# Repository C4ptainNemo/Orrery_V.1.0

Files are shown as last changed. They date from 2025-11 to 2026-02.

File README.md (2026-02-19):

# Orrery Version 1
orrery_v1
orrery_v1_no_top
orrey_v1_no_top_labeled

This repository is used to showcase the first completed version of my orrery.

The planets move on what is in escense slew rings, i.e. bearings with one of the rings having gear teeth to allow it to be driven. There are four sets of rings, each having a static ring that is mounted to the base, and two rotating rings, one per planet. These four sets of two make up the eight planets, Mercury & Venus, Earth & Mars, Jupiter & Saturn, Uranus & Neptune.

The gearing for the planets is also divided into the inner and outer planets. This is due to the large difference between their orbital periods. There is a main driving gear which meshed with different sets of gears that give the correct reduction to have accurate oribital periods. The outer planets have an additional planetary gear reducer (26 times reduction) between the main driving gear and their input gears.

---

## Thoughts and Improvements
Since each planets reducing gears are independent of each other, finding the correct gear ratios is simple, with a brute force check of combinations working fine. However this means that there are a lot of gears, since each planet has 3-5 gears to give the reduction and spacing needed. Improvements can be made to the layout of the gears to reduce the need for idler gears. 

Due to uncertaity of the ability to 3D print bevel gears, spur gears were used for the planet rings themselves. This added the limitation that there needs to be space between the adjectent rings to fit planet rings driving gear, which meant the planet ring gears were much larger than they otherwise need to be. Testing to find suiatble methods of printing bevel gears should be done to remove this issue.

A thought I had to reduce the number of gears needed is to have the reduction happen in a chain, instead of having seperate sets of gears for each planet. The difference in period between adjecent planets is around 2-3 except Mars to Jupiter which is about 6:1. So the orbital periods of each planet would be normalised by dividing its orbital period by Mercurys (so Mercury has a period of 1). So by doing the reduction in a chain, an approximately 2:1 reduction is needed coming from Uranus for Nepotune instead of 700:1.

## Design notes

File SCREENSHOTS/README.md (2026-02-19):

### Driving Gears
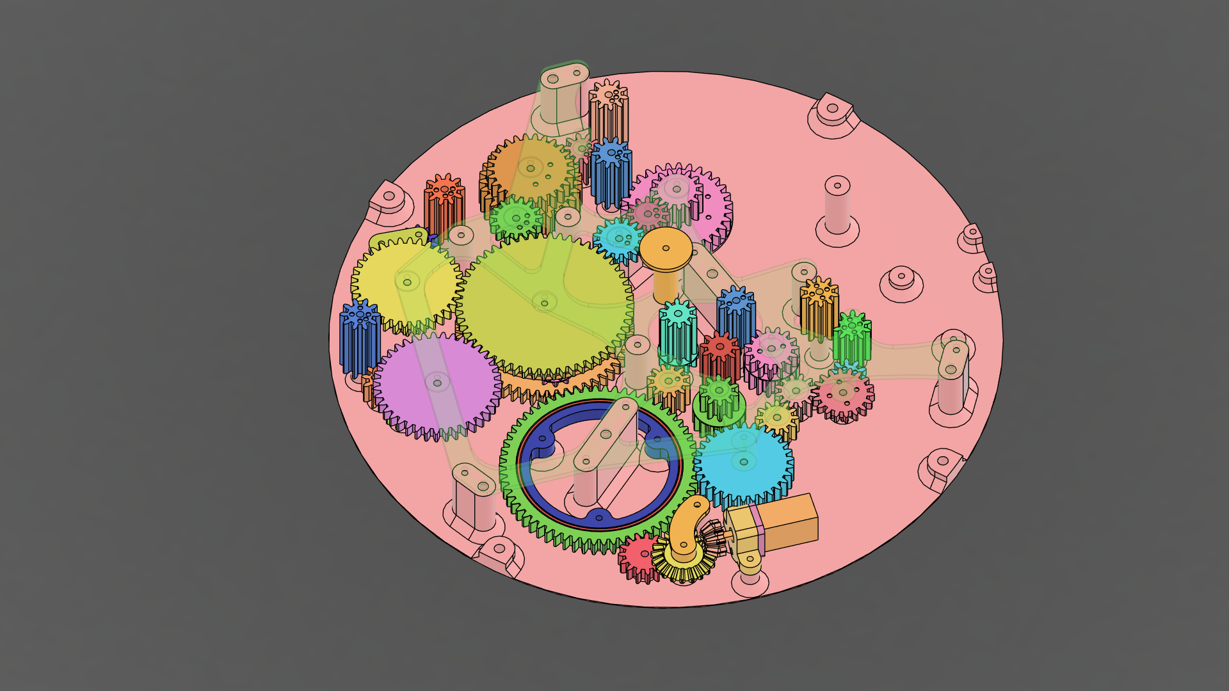
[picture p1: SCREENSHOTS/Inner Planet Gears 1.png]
Inner Planet Gears 1

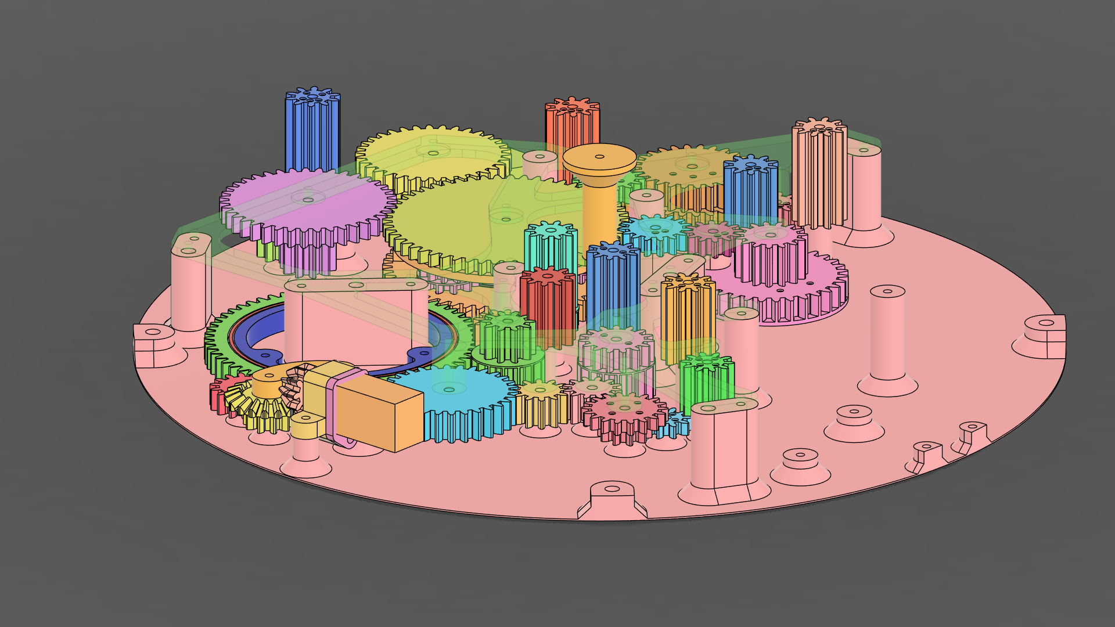
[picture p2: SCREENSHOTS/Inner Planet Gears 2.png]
Inner Planet Gears 2

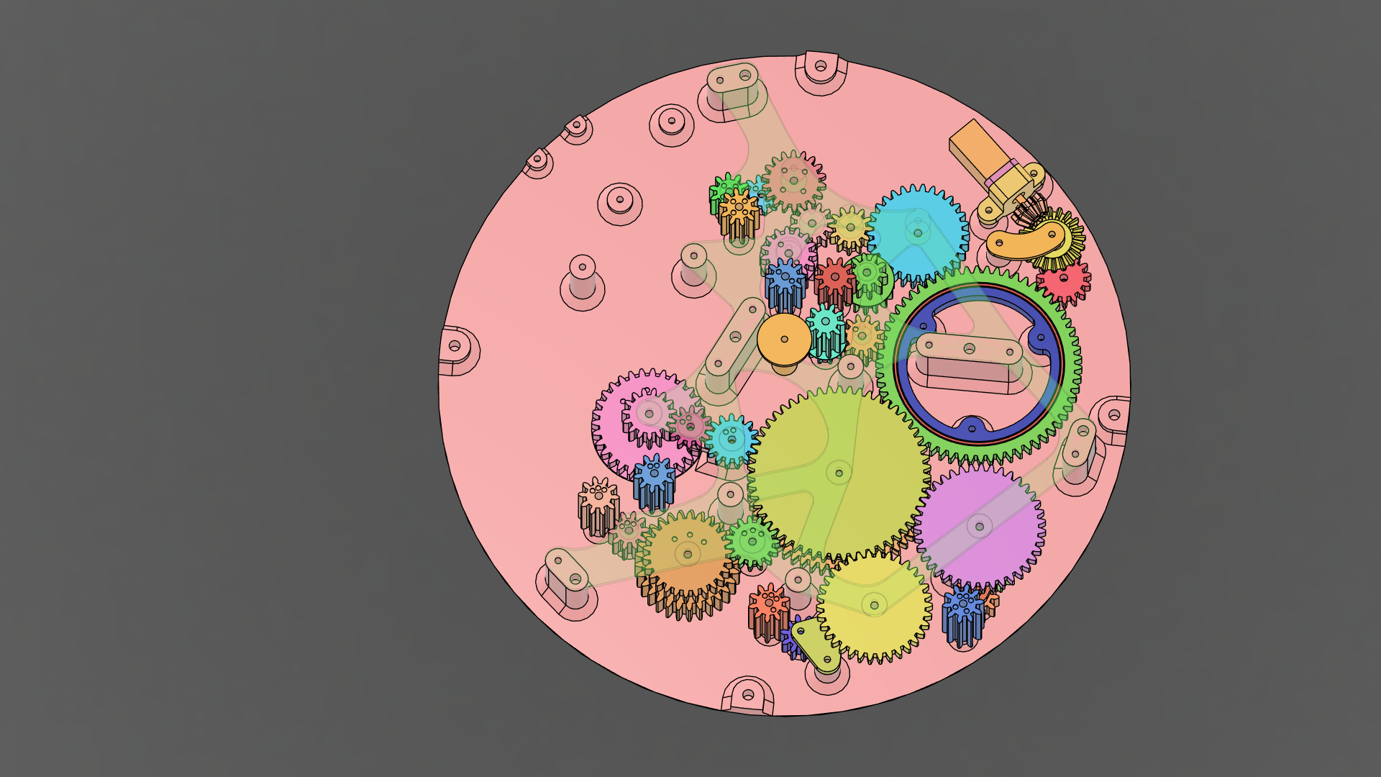
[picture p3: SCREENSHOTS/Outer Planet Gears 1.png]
Outer Planet Gears 1

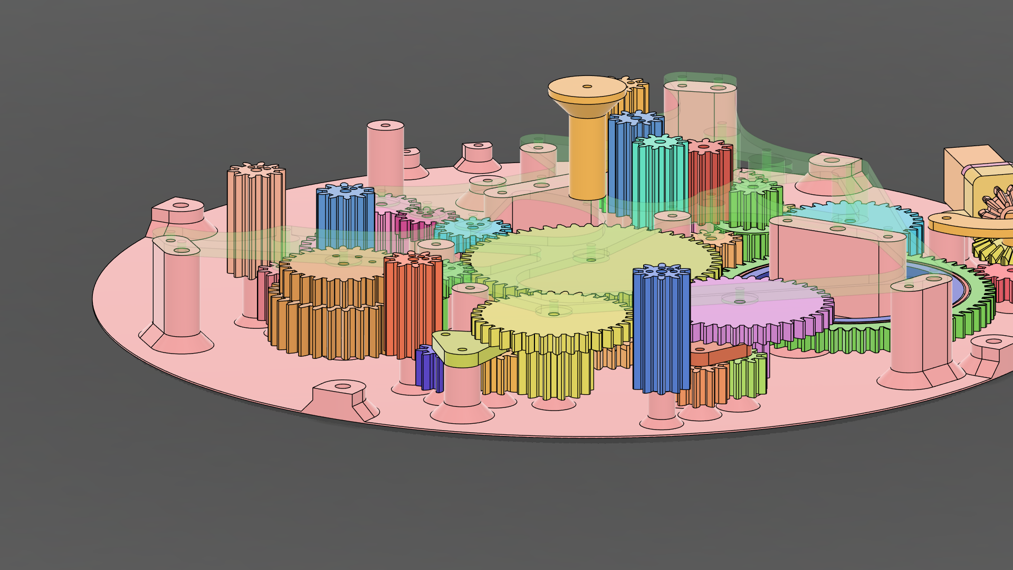
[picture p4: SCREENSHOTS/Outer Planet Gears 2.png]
Outer Planet Gears 2


---

### Ring Gears
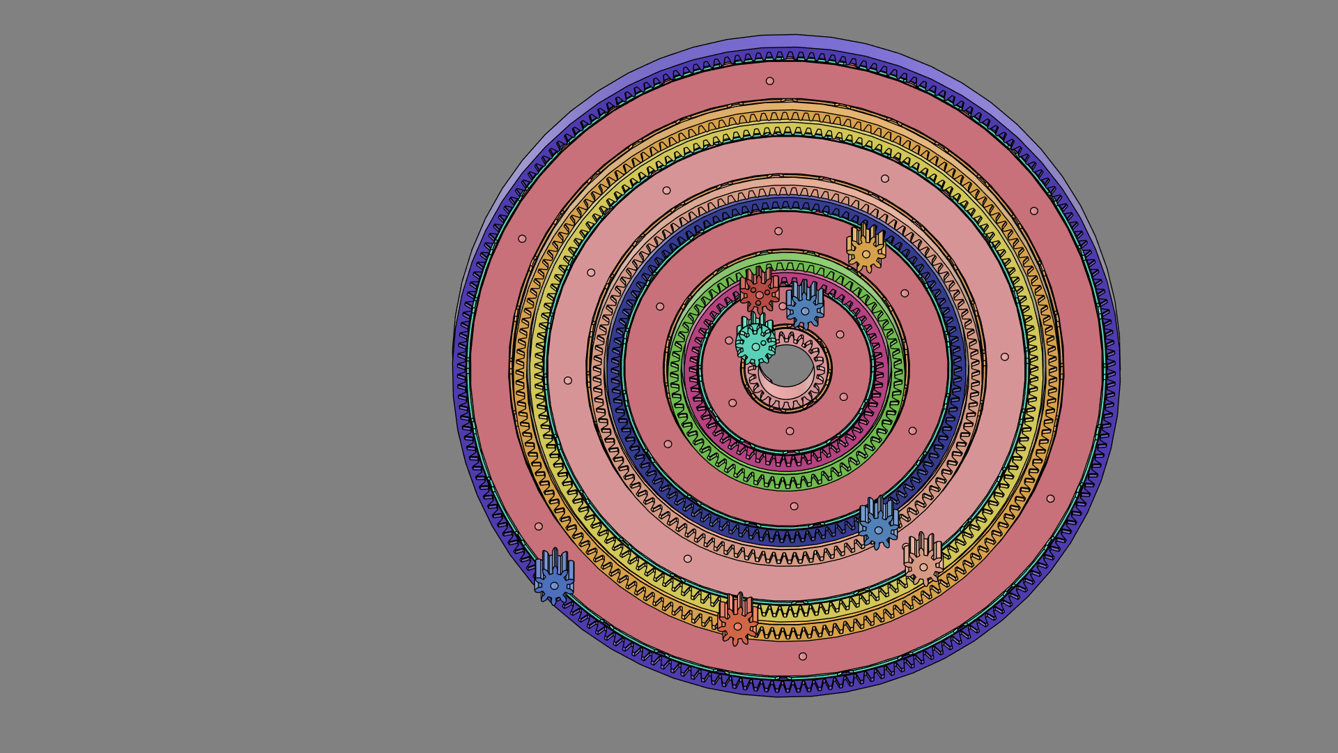
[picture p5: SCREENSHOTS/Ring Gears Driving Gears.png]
Ring Gears Driving Gears


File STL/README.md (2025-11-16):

# Orrery STL Files

## Notes and Thoughts on each type of parts

### Gears
The exteral spur gears were generated by using Fusion360's inbuilt spur gear tool and the modifying the models. The compund gears were simple, by joining two different gears into one part.

The planet ring gears were generated using a community tool {add name of tool}. These were then merged with the templete file for the ring gear assembly.

### Ring Gear Assemblies
The ring gear assembelies were made using a templete assembly that has four configurations, for Mercury & Venus, Earth & Mars, Jupiter & Saturn, Uranus & Neptune.
The configured assembly was imported into a new file and the required internal gears were joined to the appopriate blank inner and outer rings.
This didn't feel like the best way to do this. A better way would probably have been just modelling each geared ring as an indivdual part and then importing into the assembly.

The size of the rotating rings was to be as narrow as possible while allowing for a 1-1.5 modulus involute internal spur gear profile. The static rings were then sized to fill up the remaining space, so that there in as little gap as possible between the rings.
After completing the build I found it nice to watch the gears rotate. Since this is something designed to be looked at, covering the gears by having no gap between rings was definately a mistale. Each ring should be as narrow as possible to allow for the best viewing of the gears inside.

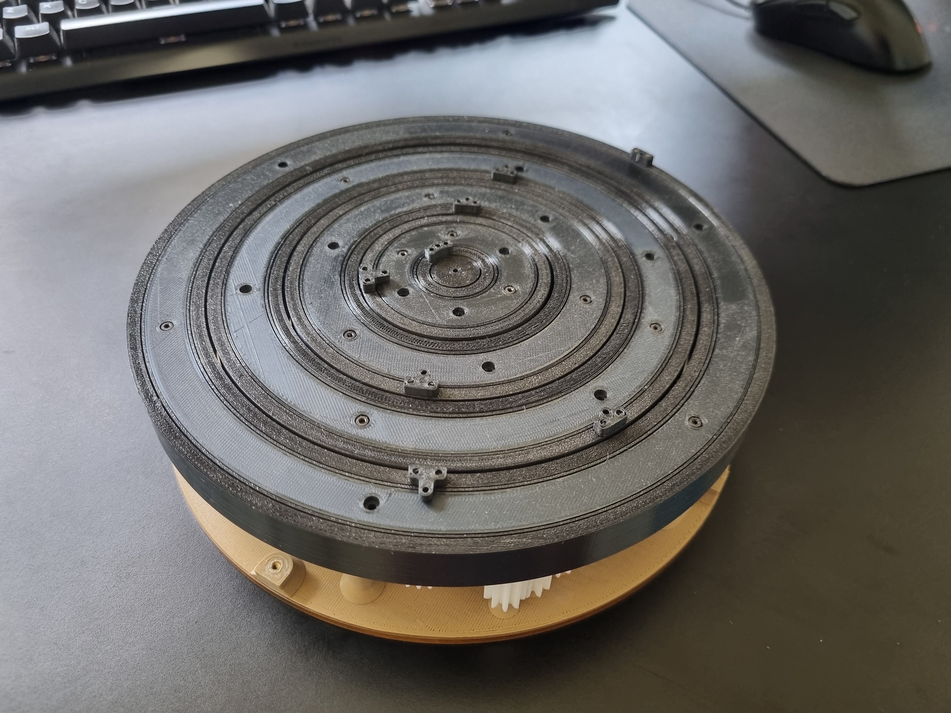
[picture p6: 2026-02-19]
PICTURES & VIDEOS/orrery_v1.jpg

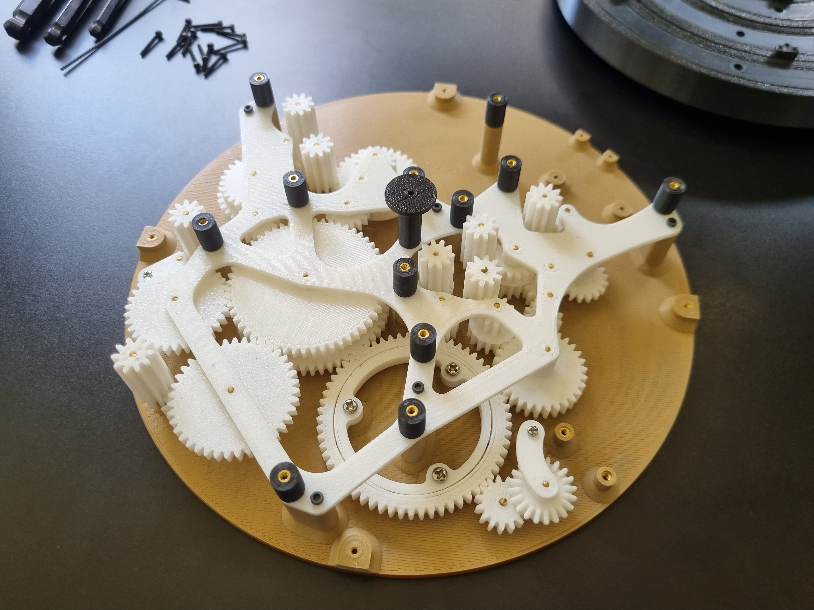
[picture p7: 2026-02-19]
PICTURES & VIDEOS/orrery_v1_no_top.jpg

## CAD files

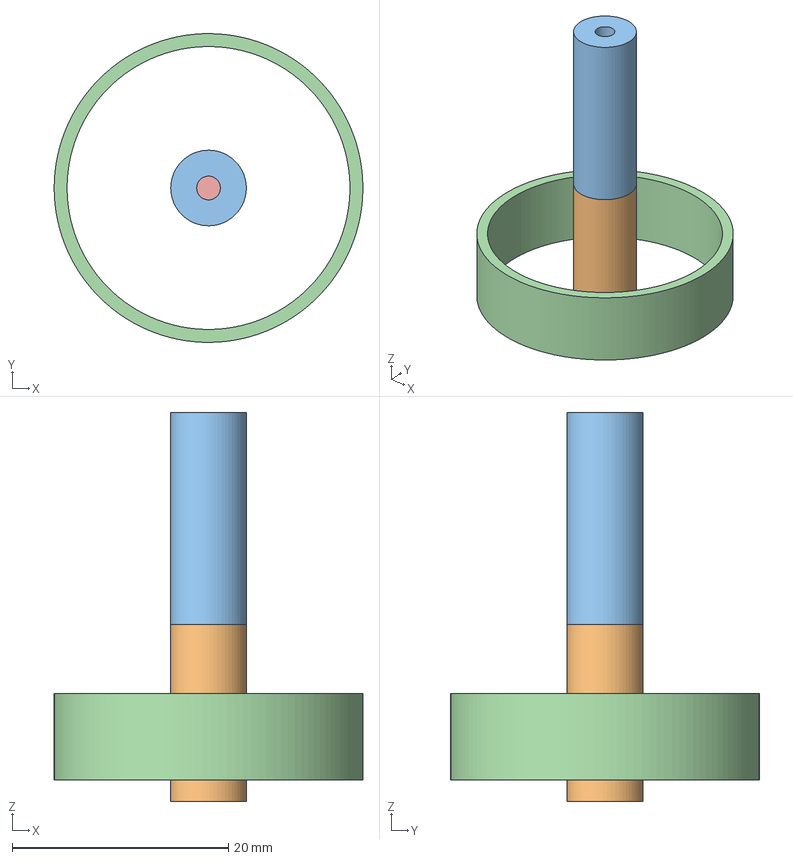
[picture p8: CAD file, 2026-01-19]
STL/Misc Assembly Tools.3mf
28.6 x 28.6 x 36.0 mm

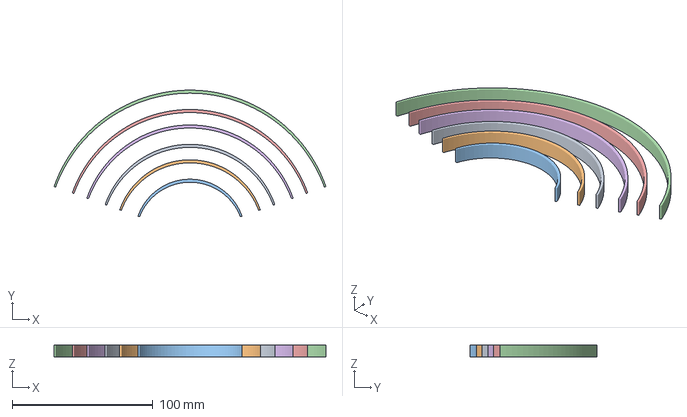
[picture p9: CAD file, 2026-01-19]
STL/Planet Ring Assembly Guides.3mf
193.2 x 90.0 x 8.80 mm

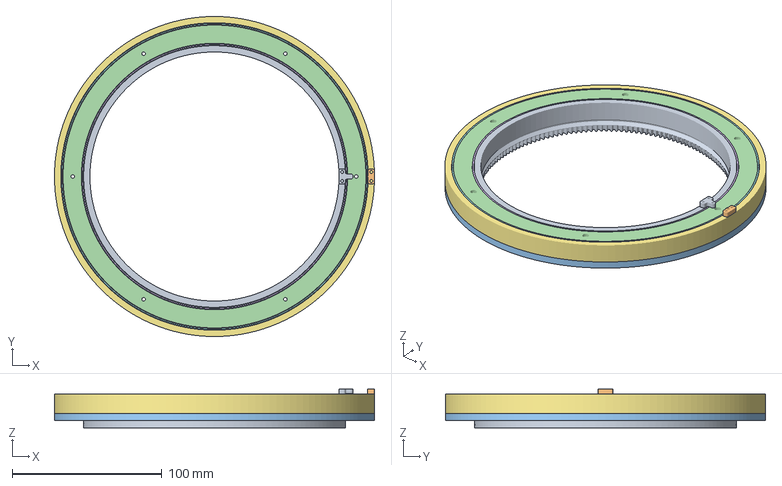
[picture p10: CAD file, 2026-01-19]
STL/Uranus-Neptune Rings.3mf
214.0 x 213.9 x 25.9 mm

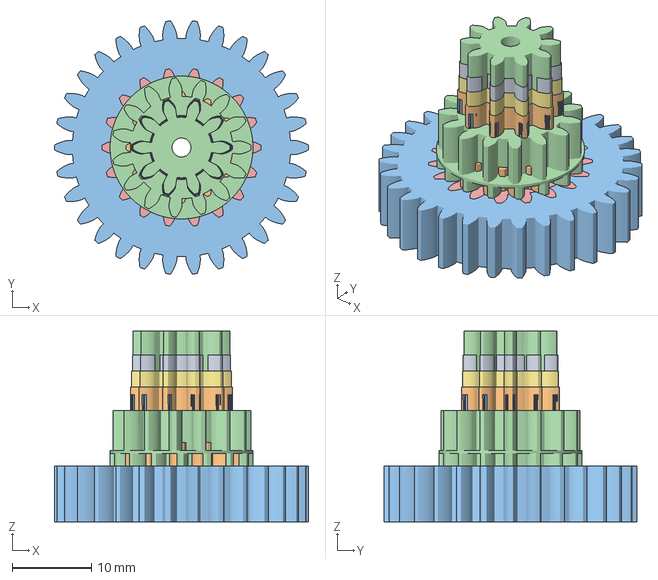
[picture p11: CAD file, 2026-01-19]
STL/Inner Planet Gears.3mf
32.0 x 31.9 x 24.0 mm

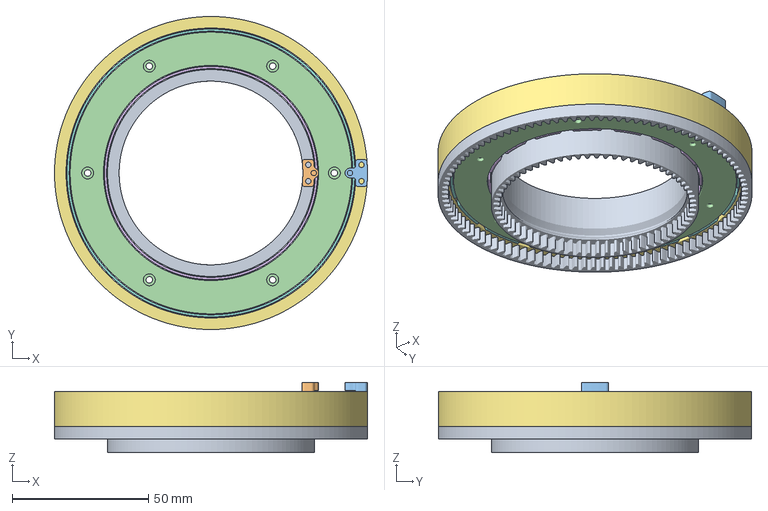
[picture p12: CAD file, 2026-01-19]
STL/Earth-Mars Rings.3mf
115.0 x 115.0 x 25.9 mm

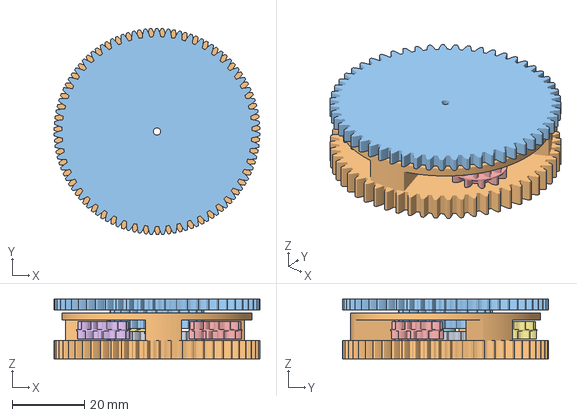
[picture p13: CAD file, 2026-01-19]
STL/22-1 Planetary Gear Reducer.3mf
57.0 x 57.0 x 16.6 mm

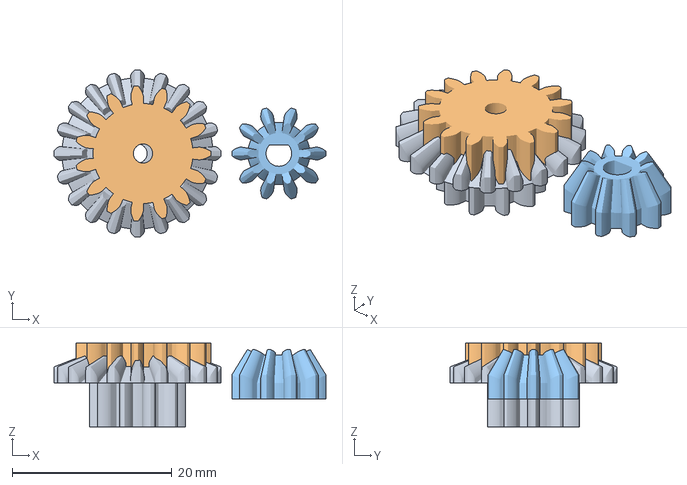
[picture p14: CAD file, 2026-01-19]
STL/Motor Input Bevel Gears.3mf
34.0 x 20.9 x 10.5 mm

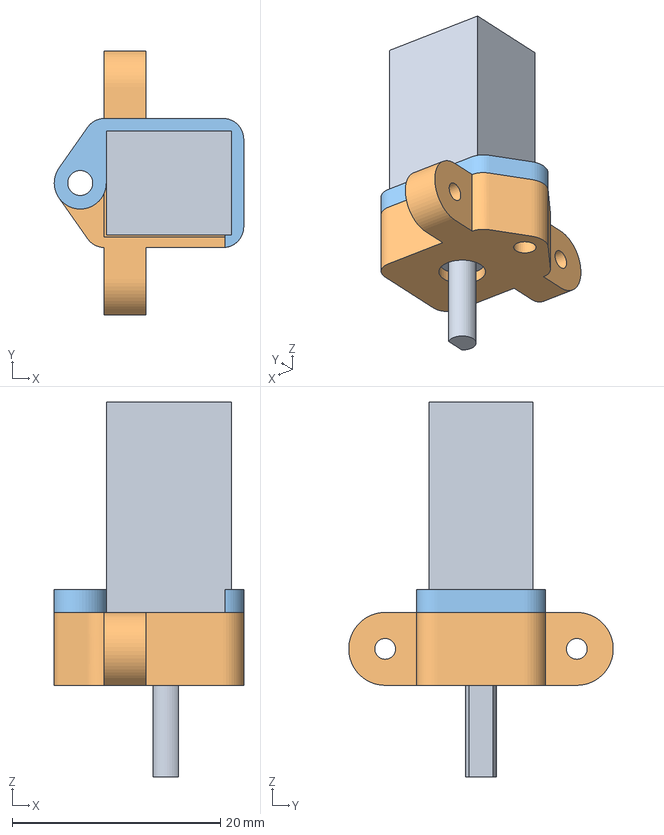
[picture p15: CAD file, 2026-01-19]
STL/Motor Case Horizontal.3mf
18.2 x 25.4 x 36.0 mm

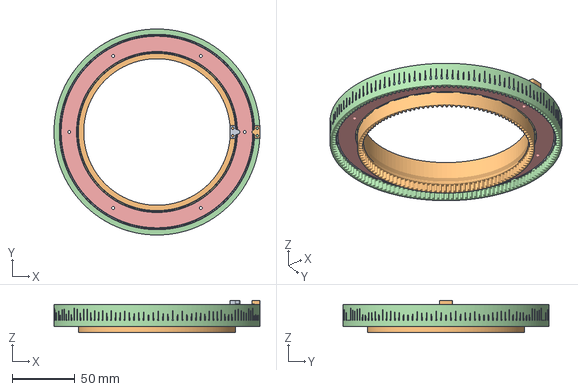
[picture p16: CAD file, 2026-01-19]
STL/Jupiter-Saturn Rings.3mf
164.5 x 164.5 x 25.9 mm

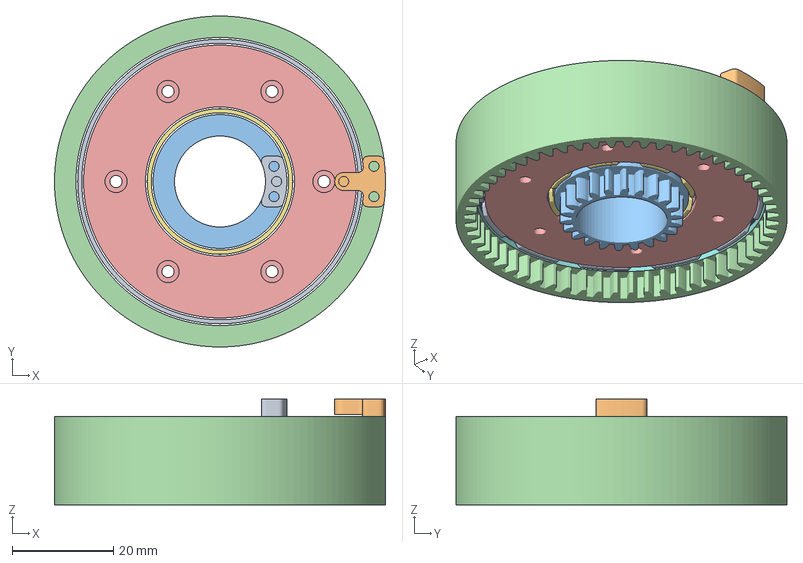
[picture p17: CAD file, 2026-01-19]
STL/Mercury-Venus Rings.3mf
65.5 x 65.5 x 20.9 mm

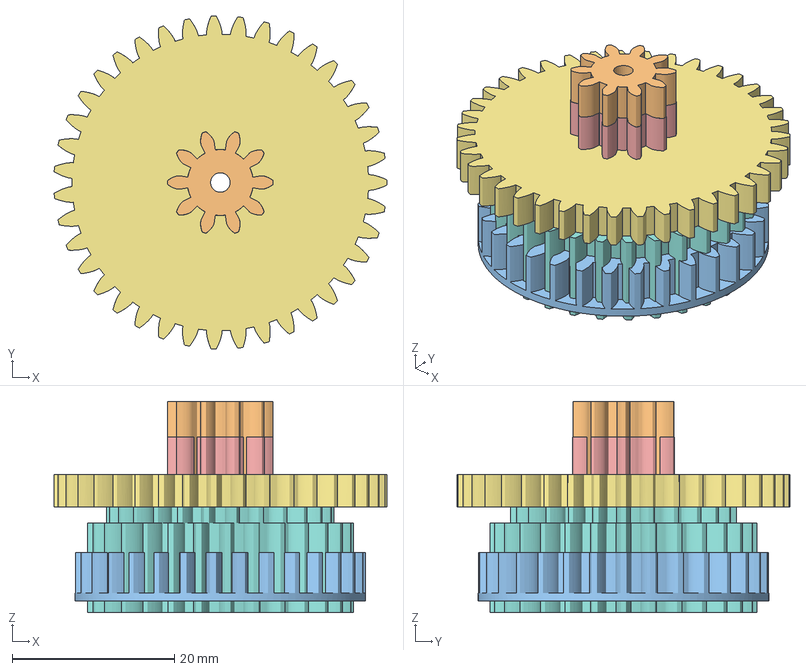
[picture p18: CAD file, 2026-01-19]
STL/Outer Planet Gears.3mf
41.0 x 41.0 x 26.0 mm

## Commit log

2025-11-16 Revise README for Orrery Version 1.0
    Expanded README to detail the orrery's design and functionality, including gear mechanisms and potential improvements.
2025-11-16 Add README for STL files of the Orrery
